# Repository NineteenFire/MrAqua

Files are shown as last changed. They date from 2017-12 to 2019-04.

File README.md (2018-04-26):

# MrAqua Aquarium Controller

This project was based off the iAqua controller written by Dan Cunningham with new features and updates here.

Controller home screen

## Features

- Water temperature monitoring
  - Allows calibration
  - Automatic shutoff of heater if water exceeds setpoint
- Automatic water top-off 
  - Float switch inputs for tank and reservoir
  - Set maximum run-time with alarm flagged if exceeded
- Feeding mode
  - Monitor time since last fed
  - Control outlets during feeding (ie turn off pumps)
- Light control 
  - 6-channel PWM or IR control of e-series LED
  - 4 lighting levels (moonlight, sunrise, mid-morning and full daylight)
- Dosing
  - 3 channels
  - Individual settings for each channel
- 8 power outlet control
  - Manual control or set on/off times
  - Aux outlets can be set to cycle times (ie on 10 minutes every 2 hours)

## Hardware

- Arduino Mega
- 320 x 240 LCD
- Arduino Mega TFT Shield (or custom shield below)
- 12V power supply
- 8 channel relay board
- DS18B20 temperature sensor
- Peristaltic pumps
- Float switch
- Submersible 12V pump
- (Optional)PCA9685 breakout board

## Libraries

- [Adafruit PWM Servo Driver](https://github.com/adafruit/Adafruit-PWM-Servo-Driver-Library)
- [Dallas Temperature](https://github.com/milesburton/Arduino-Temperature-Control-Library)
- [Time Library](https://github.com/PaulStoffregen/Time)
- [Arduino IR Remote](https://github.com/z3t0/Arduino-IRremote)
- [DS1307RTC](https://github.com/PaulStoffregen/DS1307RTC)
- [SdFat](https://github.com/greiman/SdFat)
- [TimeAlarms](https://github.com/PaulStoffregen/TimeAlarms)
- [UTFT](http://www.rinkydinkelectronics.com/library.php?id=51)
- [UTFT_SdRaw](https://platformio.org/lib/show/565/UTFT_SdRaw)
- [URTouch](http://www.rinkydinkelectronics.com/library.php?id=92)

## Setup

If you are using an ecoxotic e-series LED set "lightCSP" to true, otherwise set it to false.  If you are using a PCA9685 chip for PWM set boolean "PCA9685Installed" to true.

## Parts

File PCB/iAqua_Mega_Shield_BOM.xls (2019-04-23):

Designator | DK# | part_value | Quantity
IR1 |  | IR Transmitter | 1
U1 |  | Mega 2560 | 1
U2, U3, U4, U5, U6 | 296-26482-5-ND | 74HC541PW | 5
U12, U13 | 296-27172-1-ND | ULN2003ANSR | 2
C8, C13 | 311-1458-1-ND | 1u | 2
C12, C14 | 399-6098-ND | 47u | 2
Q3 | 475-1437-ND | SFH 300-3/4 | 1
C7 | 490-1799-1-ND | 2u2 | 1
U8 | 497-7253-1-ND | L7805ACD2T-TR | 1
U10 | 497-14661-1-ND | LDF33DT-TR | 1
U9 | 568-8366-5-ND | PCA9685 | 1
ATO, Fan1, Fan2, FloatSwitch1, FloatSwitch2, J2, Pump1, Pump2, Pump3 | 609-3918-ND | 2Pin Terminal Block | 9
P3, P4 | 609-3926-ND | 10Pin Terminal Block | 2
C1, C2, C3, C4, C5, C6, C9, C11 | 1276-1003-1-ND | 100n | 8
C10 | 1276-1123-1-ND | 330n | 1
B1 | 3001K-ND | 3001 | 1
D1, D7 | B340A-FDICT-ND | B340A-13-F | 2
Q4 | DMN3032LE-13DICT-ND | DMN3032LE-13 | 1
U7 | DS1307Z+T&RCT-ND | DS1307 | 1
U11 | MCP9701AT-E/TTCT-ND | MCP9701AT-E/TT | 1
Q1 | MMBT2222AFSCT-ND | MMBT2222A | 1
Q2 | MMBT2907AFSCT-ND | MMBT2907A | 1
R9, R10, R20, R22, R32, R33 | P1.0KACT-ND | 1K0 | 6
R1, R11 | P4.7KACT-ND | 4K7 | 2
R21 | P10ACT-ND | 10R0 | 1
R4, R5, R12, R13, R14, R15, R16, R24, R30, R34 | P10KACT-ND | 10K0 | 10
R2, R3, R28, R35, R36, R37, R38, R39, R40 | P100ACT-ND | 100R | 9
R27 | P100KACT-ND | 100K | 1
R23 | P499CCT-ND | 499R | 1
JP1 | S1011EC-03-ND | 3pin header | 1
P1, P2 | S1011EC-03-ND | 3pin header | 2
P10 | S1011EC-10-ND | 10Pin Header | 1
HD1, HS1, HS2 | S2012EC-18-ND, A113648-ND | 38 pin header, 40 pin single row header | 3
P9 | S6104-ND | PRPC020DAAN-RC | 1
Y1 | X1123-ND | ECS-3X8X | 1

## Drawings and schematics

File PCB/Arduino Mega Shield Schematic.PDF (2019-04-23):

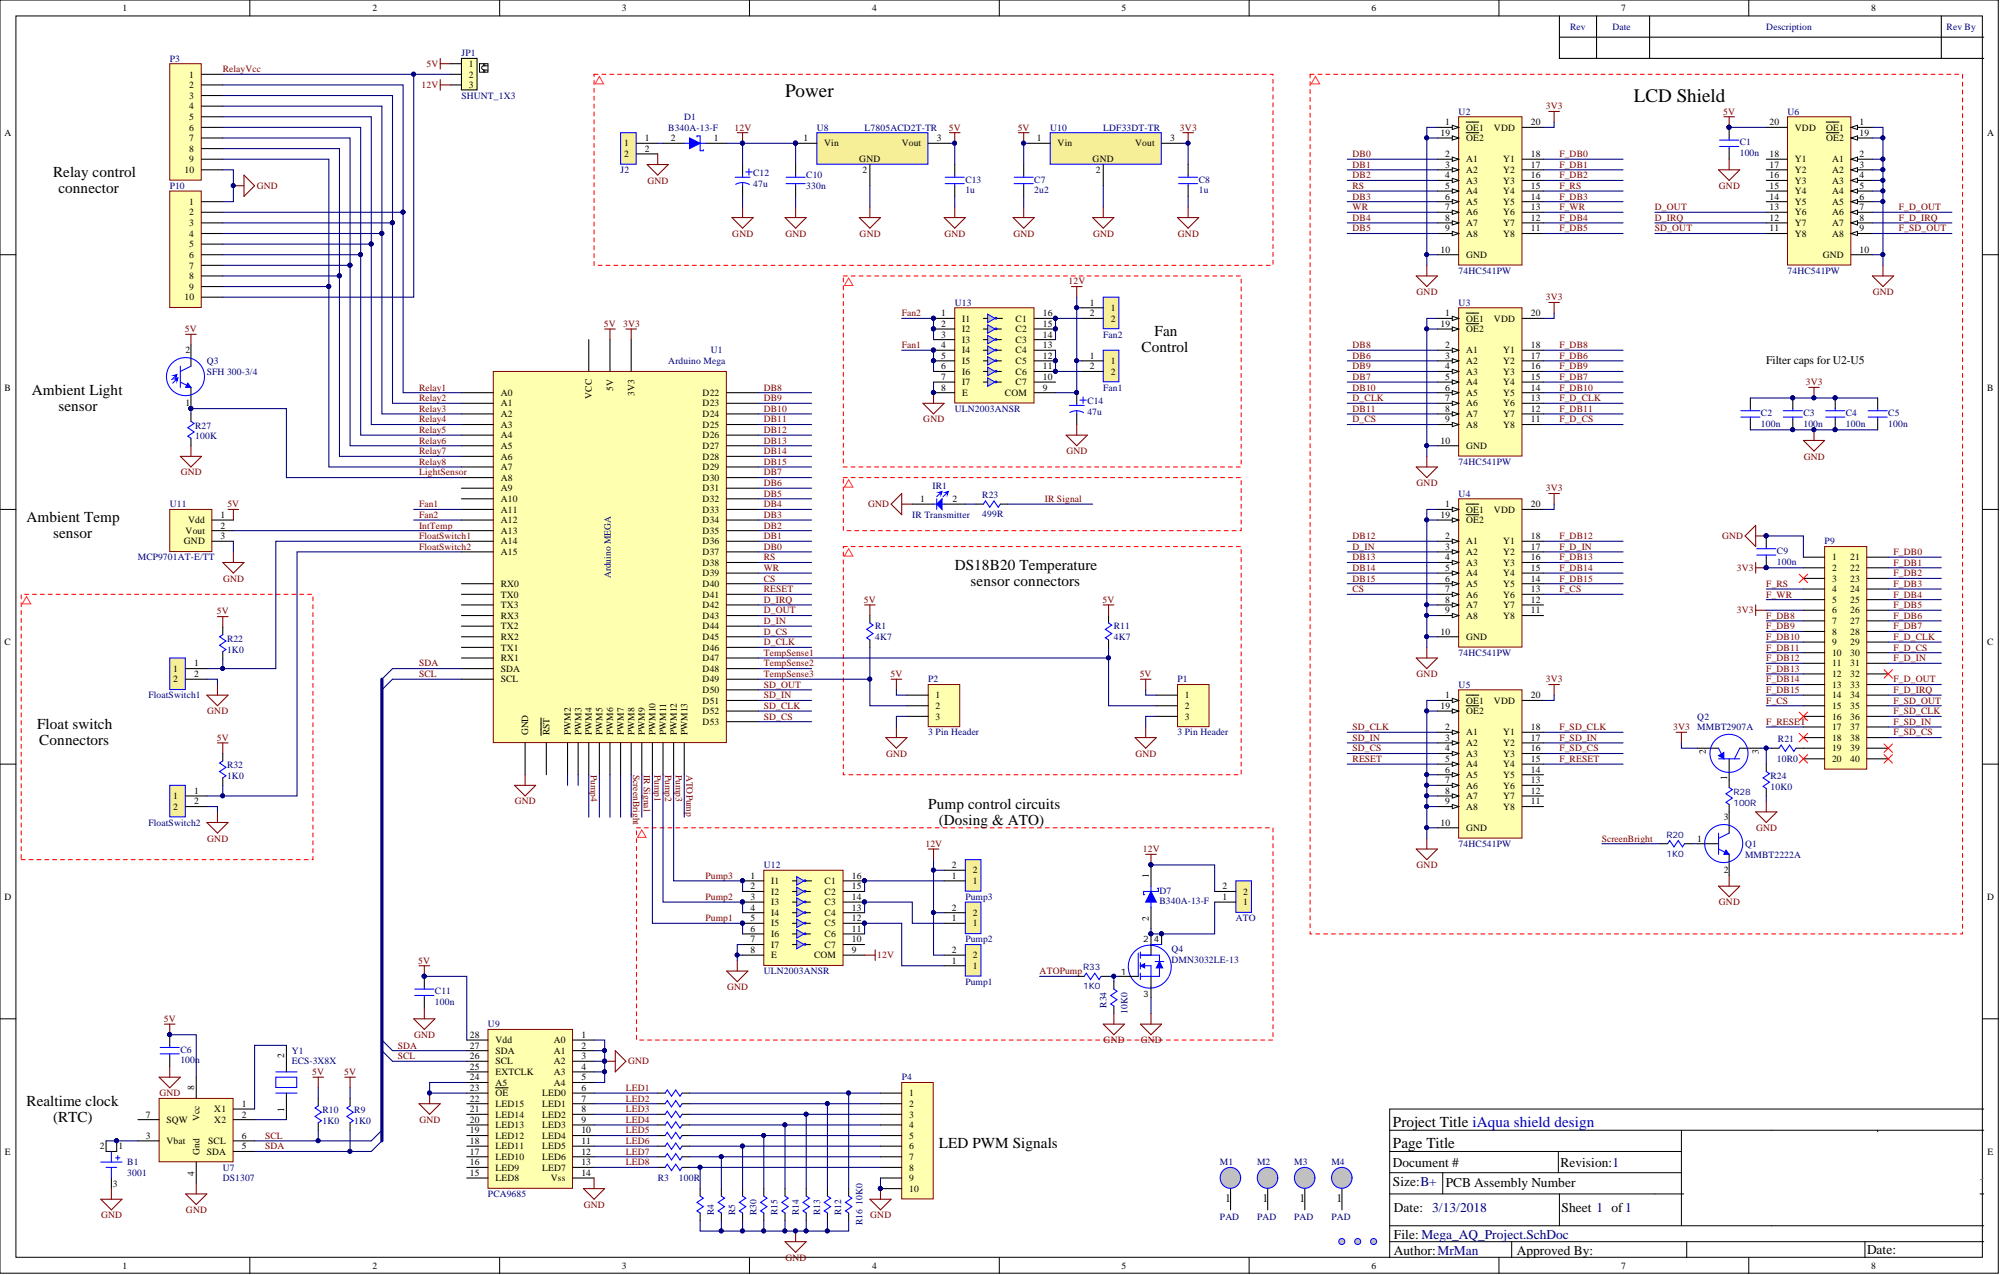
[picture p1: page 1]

2 | D R3 2 | SCL

Page Title | Del ta-Q Technologies Corp. 3755 Wi l l ingdon Bri t ish Columbi | Ave Burnaby a Canada, V5G 3H3 | CO NFIDENTIA PROPRIETARY

# | Revision: 1
B+ | PCB Assembly Number
Date: 3/13/2018 | Sheet 1 of 1 | The information contained in this dr awing is the sole prope rty of Delta -Q T e chnologie s Corp. Any r eproduction in whole or in pa rt without the written pe rmis sion of Delta -Q T e chnologie s Corp. is prohibite d

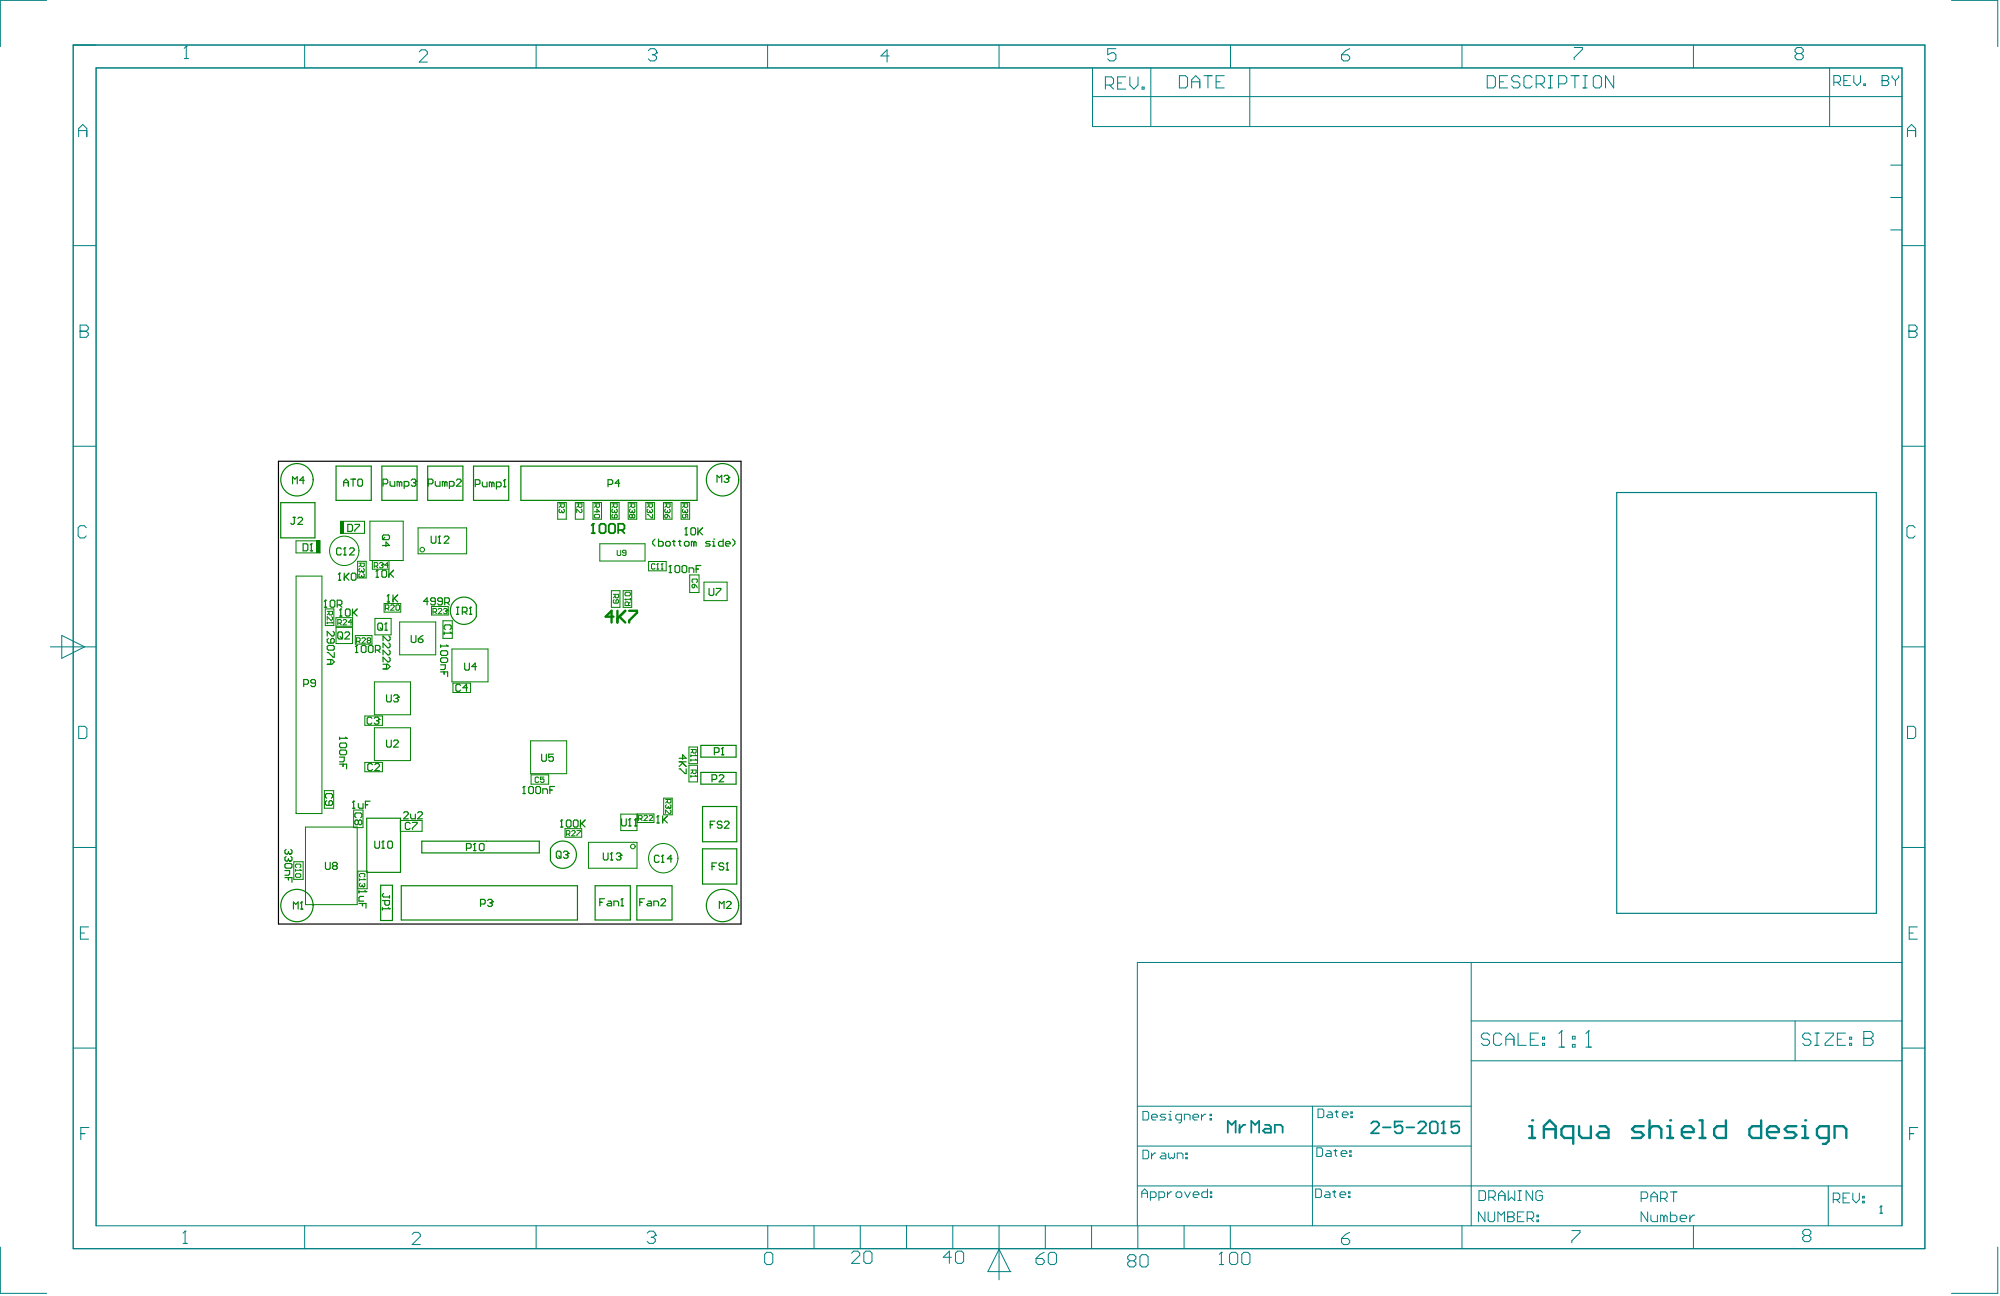
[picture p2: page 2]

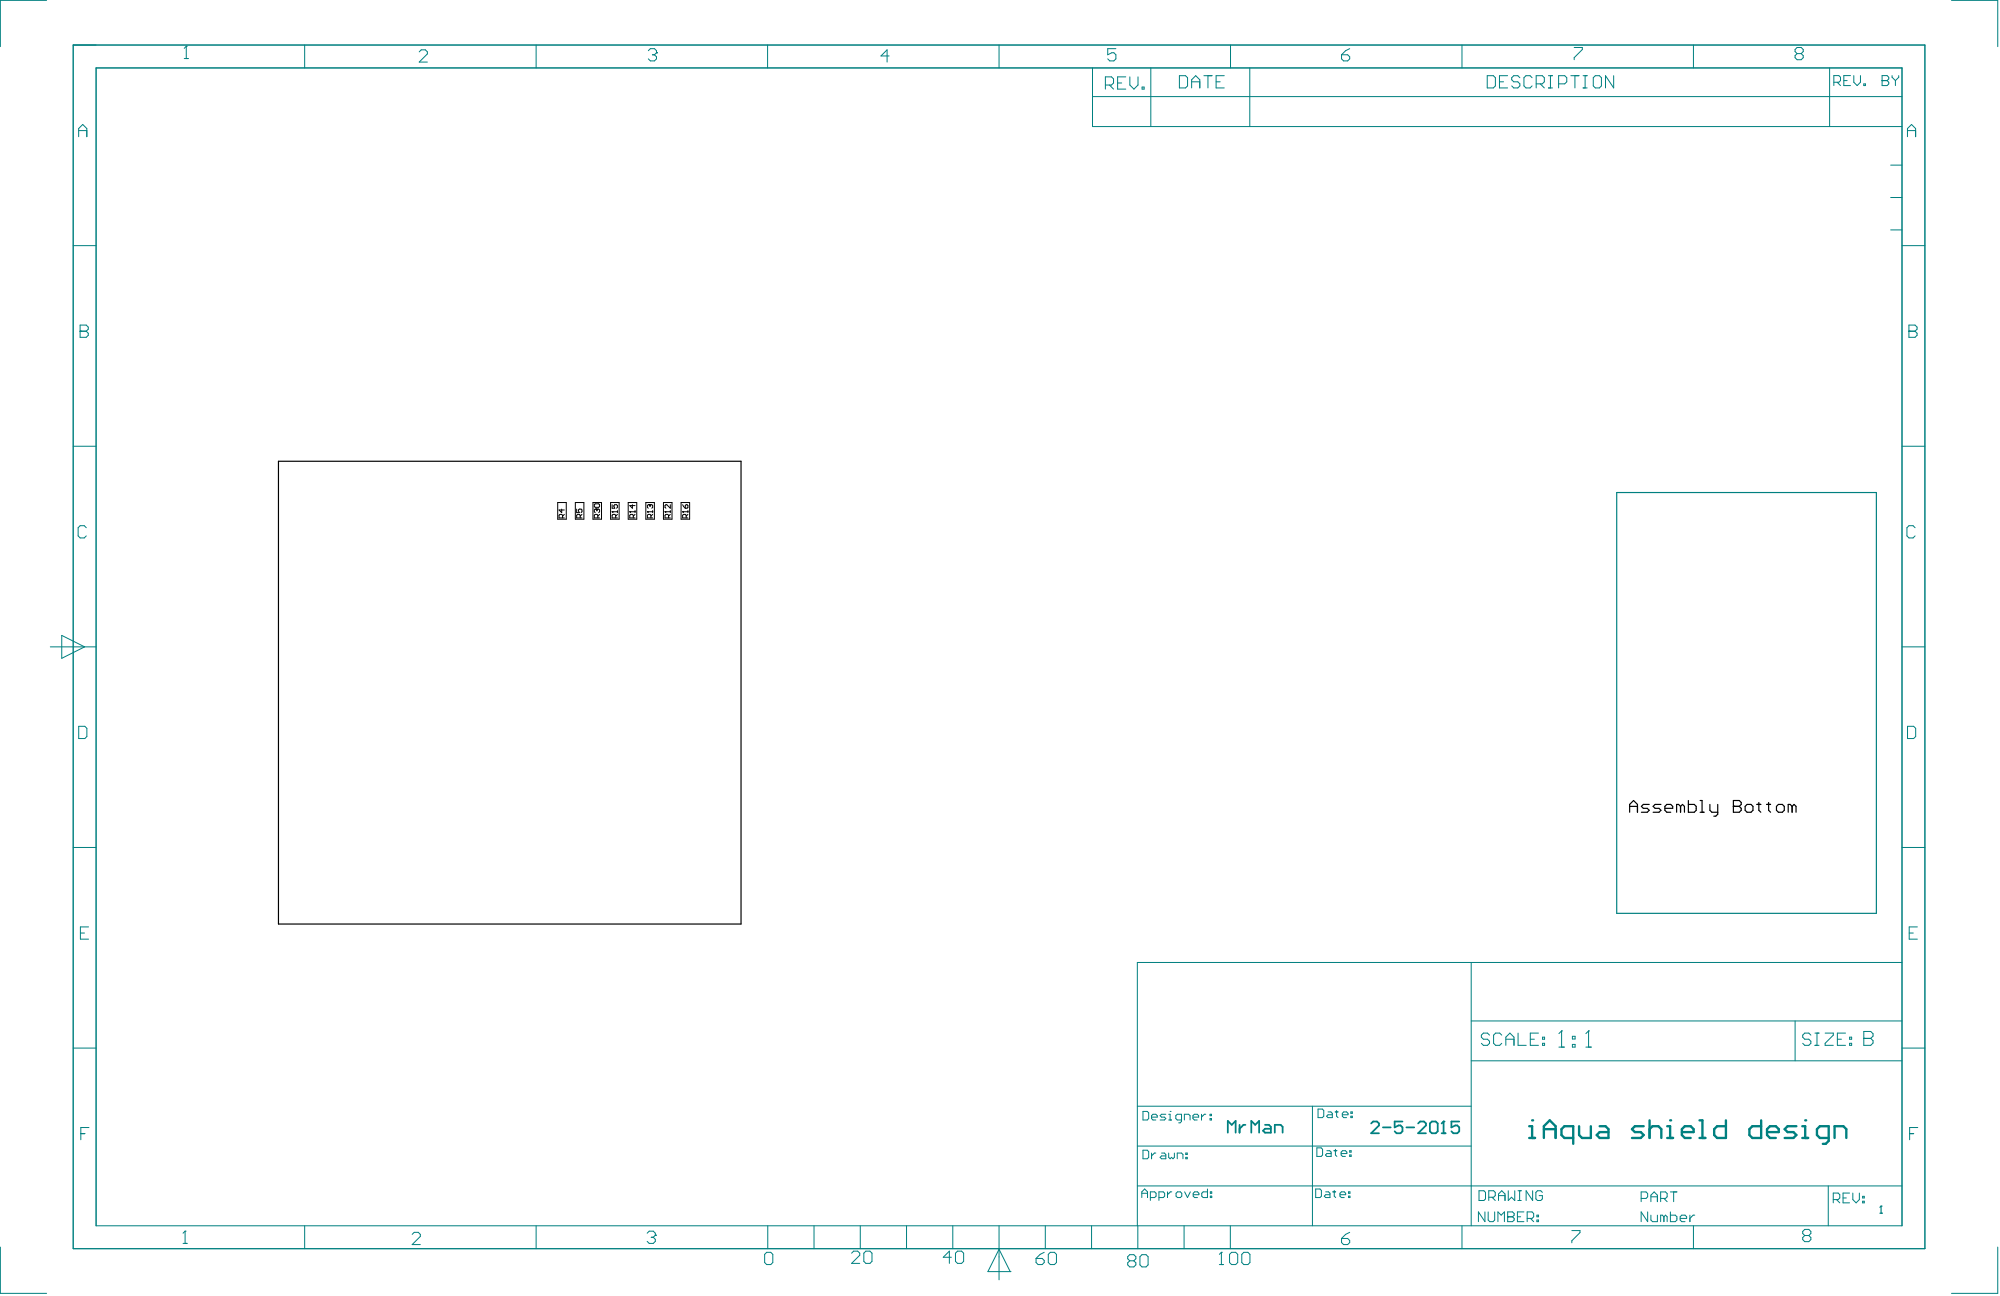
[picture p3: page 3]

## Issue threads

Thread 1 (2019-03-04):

Please include the PCB and BOM here

WZ9V, 2019-03-04:
It would be nice if the PCB and BOM files were here also instead of having to dig them out of the very long thread on PlantedTank.

NineteenFire, 2019-04-23:
Done

Closed 2019-04-23.

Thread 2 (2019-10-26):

Documentation/build thread?

Sokonomi, 2019-10-26:
Is there a thread somewhere that shows how to build this device?

rajdude, 2020-06-19:
I am also looking for the same information. I Googled this up and down but so far, have not found anything. Other than the original thread, which this code is based on there seems to be nothing out there

https://www.plantedtank.net/forums/20-diy/677265-iaqua-my-touch-interface-aquarium-controller-arduino.html

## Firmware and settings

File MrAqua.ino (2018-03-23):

/*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
 * 2. Redistributions in binary form must reproduce the above copyright
 *    notice, this list of conditions and the following disclaimer in the
 *    documentation and/or other materials provided with the distribution.

 * THIS SOFTWARE IS PROVIDED BY THE CONTRIBUTORS "AS IS" AND ANY EXPRESS OR 
 * IMPLIED WARRANTIES, INCLUDING, BUT NOT LIMITED TO, THE IMPLIED WARRANTIES 
 * OF MERCHANTABILITY AND FITNESS FOR A PARTICULAR PURPOSE ARE DISCLAIMED. IN
 * NO EVENT SHALL THE CONTRIBUTORS BE LIABLE FOR ANY DIRECT, INDIRECT, INCIDENTAL,
 * SPECIAL, EXEMPLARY, OR CONSEQUENTIAL DAMAGES (INCLUDING, BUT NOT LIMITED TO, 
 * PROCUREMENT OF SUBSTITUTE GOODS OR SERVICES; LOSS OF USE, DATA, OR PROFITS; OR 
 * BUSINESS INTERRUPTION) HOWEVER CAUSED AND ON ANY THEORY OF LIABILITY, WHETHER IN
 * CONTRACT, STRICT LIABILITY, OR TORT (INCLUDING NEGLIGENCE OR OTHERWISE)
 * ARISING IN ANY WAY OUT OF THE USE OF THIS SOFTWARE, EVEN IF ADVISED OF THE
 * POSSIBILITY OF SUCH DAMAGE.  
 */

// iAqua Aquarium Controller w/ iPhone-like Interface
// Written by Dan Cunningham, aka AnotherHobby @ plantedtank.net
// Various updates added by Ryan Truss, aka MrMan
// Much code was swiped, modified, and integrated or otherwise inspired from other public works
// All code is public domain, feel free to use, abuse, edit, and share
// Written for Arduino Mega 2560
//
// MrAqua v2.5.3
// -Fixed feeding restart button to only re-start timer
// -Updated screen setting menu to update brightness as it's changed rather than waiting till it
//  dims and then goes bright at a touch
//
// MrAqua v2.5.2
// -Updated feeding to allow not including outlets in feeding routine
// -Updated homescreen ATO display (empty reservoir shows as alarm instead of always displaying)
//
// MrAqua v2.5.0
// -Added watchdog to reset MCU on code freezing
// -Fixed bug where aux1 in timer mode would turn off aux2
// -Updated feeding screen/home screen to show exact time remaining instead of <x minutes
// -Swapped CO2 and Heater pin/icon locations, search for "swapped" to find all instaces and revert
// -Added code to use Serial2 to send/receive information from remote LED module (send LED values, 
//  fan state, reading LED heatsink temperature and request for LED values)
//
// MrAqua v2.4.0
// -Fix power schedule screen (45 degree text is unreadable)
// -Update auto-dimming to use an idle after x minutes timer instead of reading ambient light
// -Home screen now shows all 3 temperatures at the same time if more than just water sensor is enabled
//
// MrAqua v2.3.6
// -Add ability for Aux1 and Aux2 to be used as repeated timer rather than single 24Hr schedule
// -Updated some of the check boxes to on/off icon to fit with theme of the program
// -Updated power alarm behaviours during feeding to avoid devices turning on/off when they shouldn't
//
// MrAqua v2.3.5
// -Fixed startup where outputs would be ON but display showing them OFF
// -Added manual ATO turn-on by pressing section on home screen (runs for max run time)
//
// MrAqua v2.3.3 / 2.3.4
// -Fixed some bugs including heatsink temp sensor using wrong pin, dosing amount limits and PCB temp 
//  sensor not able to read in degrees F
//
// MrAqua v2.3.2
// -Added seperate screen function for IR lights using up/down arrows
// -Dosing alarms now trigger the start but main loop turns them off.  This way the program doesn't
//  freeze when it starts to dose
// -Corrected heatsink temp sensor to use correct device address
//
// MrAqua v2.3.1
// -Added code from alphabeta to add a second on/off schedule for lights
// -Updated light values/system so stored values are always 0-100
// -Updated home screen dosing to correctly draw tubes and not allow remaining volume to go below 0
//
// MrAqua 
// -Updated feeding routine to only toggle filter/pump/aux outputs
// -Added graph display for LED channels 
// -Added routine writeToLED(channel,value) to handle writing to either PCA or Mega PWM pins
// -Modified LED PWM code to optionally use PCA9685 for 12-bit dimming
// -Added 5th/6th LED channel, moved EEPROM for LED values to 400's
// -Added lunar cycle control
// -Added probe settings menu to enable/disable temp sensors and change display units between C and F
// -Added sub-settings menus for sensors to control when fans turn on/off (external fan 
//  controlled by heatsink sensor, internal fan controlled by internal temp) or heater in case of
//  probe 1.  Also added calibration offset for probes
// -Changed feeding, update time and screen dim tracking to using RTC instead of millis 
//  (millis only used for tracking touch timing for better resolution)
// -Changed code for 3 pumps, reworked schedule and setting screens to select a pump and then
//  individual pump dose amounts
// -Added code for ATO
// -Changed LED color setting to bargraph (0-100%) instead of up/down button
// -Added color setting menu for changing bargraph colors
// -Added routine for sending commands to sat+ with the updated bargraphs
// -switched RTClib to DS1307RTC library
// -switched to sdfat and utft_sdraw library for accessing SD card files (can use larger SD 
//  cards and has faster loading speeds)
// -Added read of displayInCelcius to startup
// -Added boolean displayIn12Hr to change clock to 24Hr/12Hr
//
// Original iAqua revision documentation:
// CURRENT VERSION 1.0.4
// - the smart startup routine has been reworked and fixed by robsworld78 at The Planted Tank forums!
// - added a first run routine that will zero out all EEPROM data that is needed by iAqua
//
// VERSION 1.0.3
// - fixed smartstartup routine bugs
// - fixed dosing display when resevoir goes negative due to forgettig to hit fill
// - added robsworld78 at The Planted Tank's PWM smart startup lighting code
// - fixed issue when temp turned red, and then turned feeding time red
//
// VERSION:  1.0.2
// - more accurate math for how doses were calcualted on home screen
// - updated power schedules to update home screen immediately
// - day name was off using new RTC and Time library
//
// VERSION:  1.0.1
// - created smart startup routine
// - fixed math bug with dosing pump speed saving to eeprom
// - changed PWM pins for dosing pumps to make room for RGBW PWM pins
// - changed from previous RTC library to RTClib.h
//
// VERSION:  1.0
// - initial version
//
// EEPROM locations (saved settings)
// SPACE // DESCRIPTION
// 0 // 
// 1 // feeding enable filter
// 2 // feeding enable circ
// 3 // feeding enable heat
// 4 // feeding enable co2
// 5 // feeding enable aux 1
// 6 // feeding enable aux 2
// 7 // feeding minutes setting
// 8 // feeding  light 1 (0 off, 1 on)
// 9 // feeding pwr light 2 (0 off, 1 on)
// 10 // feeding pwr filter (0 off, 1 on)
// 11 // feeding pwr circ (0 off, 1 on)
// 12 // feeding pwr heat (0 off, 1 on)
// 13 // feeding pwr co2 (0 off, 1 on)
// 14 // feeding pwr aux 1 (0 off, 1 on)
// 15 // feeding pwr aux 2 (0 off, 1 on)
// 16 // NOT USED
// 17 // heater off temp
// 18 // heater on temp
// 19 // NOT USED
// 20 // pump 1 dose in mL
// 21 // pump 2 dose in mL
// 22 // pump 3 dose in mL
// 23 // pump 1 sec/ml
// 24 // pump 2 sec/ml
// 25 // pump 3 sec/ml
// 26 // dosing reseviors capacity in mL
// 27 // 
// 28 // screen:  return home
// 29 // screen:  autodim level
// 30 // screen:  autodim seconds
// 31 // screen:  brightness if no dim
// 32 // pump 1 remaining volume high byte ^10th
// 33 // pump 1 remaining volume low byte
// 34 // pump 2 remaining volume high byte ^10th
// 35 // pump 2 remaining volume low byte
// 36 // pump 3 remaining volume high byte ^10th
// 37 // pump 3 remaining volume low byte
// ... //
// 40 // ATO Enabled
// 41 // Reservoir switch Enabled
// 42 // Low level wait time in minutes
// 43 // Max run-time / 10
// 44 // ATO alarm flagged
// ... //
// 50 // Temp sensor 1 installed (water)
// 51 // Temp sensor 2 installed (heatsink)
// 52 // Internal sensor installed (MCP9701)
// 53 // Heatsink fan on temperature
// 54 // Heatsink fan off temperature
// 55 // Internal fan on temperature
// 56 // Internal fan off temperature
// 57 // Display in celcius?
// 58 // sensor 1 calibration offset
// 59 // sensor 2 calibration offset
// 60 // sensor 3 calibration offset
// 61 // display sensor 1 on home screen
// 62 // display sensor 2 on home screen
// 63 // display sensor 3 on home screen
// ... // 
// 70 // Lunar cycle enabled
// 71 // Clouds enabled
// 72 // Cloud start hour
// 73 // Cloud start minute
// 74 // Cloud run hours
// 75 // Cloud run minutes
// 76 // Cloud channels enabled (bit 0 = chan1, bit 1 = chan2...)
// ... //
// 80 // bar 1 color
// 81 // bar 2 color
// 82 // bar 3 color
// 83 // bar 4 color
// 84 // bar 5 color
// 85 // bar 6 color
// 86 // bar 7 color
// 87 // bar 8 color
// 88 // bar 9 color
// ... //
// 100-139 // power scheudle
// 220-243 // light ramp schedule
// 280-284 // light bar colors
// 300 // pump1 onHour
// 301 // pump1 onMin
// 302 // pump1 SUN
// 303 // pump1 MON
// 304 // pump1 TUE
// 305 // pump1 WED
// 306 // pump1 THUR
// 307 // pump1 FRI
// 308 // pump1 SAT
// 309-317 // pump2
// 318-326 // pump3
// ... //
// 400+ // LED values

#include <avr/wdt.h> //added for WDT
#include <Wire.h> // needed by tons of stuff
#include <EEPROM.h>  // used to store and retrieve settings from memory
#include <UTFT.h>  // used to interface with the TFT display
#include <SdFat.h>
#include <UTFT_SdRaw.h>
#include <URTouch.h>  // used to interface with the touch controller on the TFT display
#include <DS1307RTC.h>
//#include <DS3232RTC.h>
#include <TimeLib.h>
#include <TimeAlarms.h>  // used to power schedules
#include <IRremote.h>  // used to send IR commands to the light, LED must be on pin 9
#include <OneWire.h> // network library to communicate with the DallasTemperature sensor, 
#include <DallasTemperature.h>  // library for the Temp sensor itself
#include <Adafruit_PWMServoDriver.h> //PCA9865

UTFT myGLCD(SSD1289,38,39,40,41); // start up an instance of the TFT screen
URTouch myTouch(46,45,44,43,42);  // start up an instance of for touch
//URTouch myTouch(6, 5, 4, 3, 2); // For standard TFT shield

// file system object
SdFat sd;
const byte ChipSelect = 53; // For TFT Shield
UTFT_SdRaw myFiles(&myGLCD);

// Declare which fonts we will be using
extern uint8_t Sinclair_S[];
extern uint8_t arial_bold[];

//initialize PCA9865
Adafruit_PWMServoDriver pwm = Adafruit_PWMServoDriver(0x40);

// define relay pins
const int pwrLight1Pin = A0;
const int pwrLight2Pin = A1;
const int pwrFilterPin = A2;
const int pwrCircPin = A3;
//const int pwrHeatPin = A4;  //normal operation
//const int pwrCO2Pin = A5;   //normal operation
const int pwrHeatPin = A5;//co2/heater pins swapped
const int pwrCO2Pin = A4; //co2/heater pins swapped
const int pwrAux1Pin = A6;
const int pwrAux2Pin = A7;

//define misc pins
const int lightSensorPin = A8;  // analog pin for the ambient light sensor
const int pressureSensorPin = A9;  // analog pin for the CO2 pressure sensor
const int fan1Pin = A11;
const int fan2Pin = A12;
const int internalTempPin = A13;
const int ATOFloatPin = A14;
const int TankFloatPin = A15;
const int screenBrightPin = 8; // pwm pin for the LCD backlight
//define pump pins
const int dosingPump1 = 10;
const int dosingPump2 = 11;
const int dosingPump3 = 12;
const int ATOPumpPin = 13;
// define RGBW PWM pins
const int led1Pin = 2;
const int led2Pin = 3;
const int led3Pin = 4;
const int led4Pin = 5;
const int led5Pin = 6;
const int led6Pin = 7;

// Pins for temperature sensor
#define ONE_WIRE_BUS_W 47  //water sensor on pin 47
#define ONE_WIRE_BUS_H 49  //Heatsink sensor on pin 49

// Setup a oneWire instance to communicate with any OneWire devices
OneWire oneWireW(ONE_WIRE_BUS_W);
OneWire oneWireH(ONE_WIRE_BUS_H);

// Pass our oneWire reference to Dallas Temperature. 
DallasTemperature sensorW(&oneWireW);
DallasTemperature sensorH(&oneWireH);

// Device address variables
DeviceAddress waterSensor;
DeviceAddress heatsinkSensor;

// create an IR instance
IRsend irsend;

byte dispScreen=0;    // screens are listed below
//1-home
//    2-feeding
//    3-power
//    4-settings
//        5 - Light Settings
//        6 - clock
//        7 - feed settings
//        18- sensor settings
//            8 - heater settings
//            19- heatsink fan settings
//            20- internal fan settings
//        9 - Schedule
//            11 - Power schedule
//                12 - Power item
//            15 - Dosing
//            13 - Light ramps schedule screen
//                14 - light ramp schedule
//        10 - Dosing settings (index 1-3 for pump#)
//        16 - Screen settings
//        17 - ATO settings
//        21 - Lunar settings
//        22 - Light bargraph color settings
//        23 - LED graph
//        24 - Light Settings for IR lights

byte scheduleItem; // track which item is being scheduled
byte currentLightMode=0;  //0=high sun, 1=mid sun, 2=low sun, 3=moon, 4=transition, 5=unknown
byte lightEditing=0;  // track if we are actively editing lights

// the next 5 variables will be set at the start of a lighting fade
int fadeDurationSeconds = 0; 
unsigned long fadeStartingSeconds = 0;
unsigned long fadeTimeLeft;
boolean fadeInProgress = false;
byte fadeFromMode = 0;  //0=high sun, 1=mid sun, 2=low sun, 3=moon
byte fadeToMode = 0;  //0=high sun, 1=mid sun, 2=low sun, 3=moon

struct RGBW // for storing light intensity values
{
  unsigned int chan1;
  unsigned int chan2;
  unsigned int chan3;
  unsigned int chan4;
  unsigned int chan5;
  unsigned int chan6;
};
typedef struct RGBW LightColor;

LightColor currentColor = {
  0,0,0,0,0,0}; // The current color of the light (used for fading)
LightColor lastColor = {
  0,0,0,0,0,0};   // The previous color of the light (used for fading)
LightColor targetColor = {
  0,0,0,0,0,0}; // The target color of the light (used for fading)
LightColor tempColor = {
  0,0,0,0,0,0}; // The temporary color of the light (used for updating sat+)

LightColor lightHighSun = {
  0,0,0,0,0,0}; // store the RGBW values for the CS+ M1 button
LightColor lightMidSun = {
  0,0,0,0,0,0}; // store the RGBW values for the CS+ M2 button 
LightColor lightLowSun = {
  0,0,0,0,0,0}; // store the RGBW values for the CS+ M3 button 
LightColor lightMoon = {
  0,0,0,0,0,0}; // store the RGBW values for the CS+ M4 button 
  
//red, green, blue, white, yellow, violet, aqua
const unsigned int VGAColor[] = {0xF800, 0x07E0, 0x001F, 0xFFFF, 0xFFE0, 0xF81F, 0x07FF};

//store colours for bargraphs
byte barColors[6] = {0,1,2,3,4,5};
byte selectedChan = 0; // used for tracking which channel is selected when changing colors

// used for time
tmElements_t prevRTC, saveRTC;
boolean displayIn12Hr = true;

// used for storing power states of relays
struct PWR
{  
  byte pwrLight1;
  byte pwrLight2;
  byte pwrFilter;
  byte pwrCirc;
  byte pwrHeat;
  byte pwrCO2;
  byte pwrAux1;
  byte pwrAux2;
} 
feedPower, preFeedPower, globalPower;

// used for storing power states of relays
struct FEED
{  
  byte pwrLight1;
  byte pwrLight2;
  byte pwrFilter;
  byte pwrCirc;
  byte pwrHeat;
  byte pwrCO2;
  byte pwrAux1;
  byte pwrAux2;
} 
feedSetting;

// holds the schedule for power relays and light ramping
struct PWRSCHED
{  
  byte active;
  byte onHour;
  byte onMinute;
  byte offHour;
  byte offMinute;
  byte timer;
}
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
void loop()
{
  unsigned long currentMillis = millis(); // get current millis
  time_t currentTime = now();

  //check temperature every 10 seconds
  if(now() - lastUpdateTime >= 10)
  {
    lastUpdateTime=now();
    checkTemp();
  }
  //check ATO/feeding and update time once per second
  if(now() != lastCheckTime)
  {
    lastCheckTime=now();
    updateTimeDate(false);//passing false results in updating screen only if time or date has changed
    checkATO();
    checkFeeding();
  }
  
  //Check status of current light ramp if applicable
  checkLightRamp();
  
  // check for touch events
  if (myTouch.dataAvailable())
  {
    if (currentMillis - prevMillisTouch > touchWaitTime) // make sure it's been .X sec between touches
    {
      // set backlight touch if not already set and turn up brightness
      if (backlightTouch==false) // backlight touch is for adjusting brightness after touch
      {
        Serial.println(F("Setting backlight to Bright value"));
        backLight = map(screenBrightMem,1,10,10,255);
        analogWrite(screenBrightPin, backLight);
        backlightTouch=true;
      }
      prevMillisTouch=currentMillis; // reset the touch timer
      dimTime = currentTime; // reset screen dim timer
      homeTime = currentTime; // reset return home timer
      processMyTouch();
    }
  }
  
  // adjust brightness automatically unless touch event
  unsigned long pastSeconds;
  if (screenDimSec!=0) // if set to 0, we won't dim
  {
    if (screenDimLevel!=0) // if set to 0, we won't dim
    {
      if (backlightTouch==true)
      {
        pastSeconds = (currentTime - dimTime);
        if (pastSeconds > screenDimSec)
        {
          Serial.println(F("Reducing backlight to dim level"));
          backlightTouch=false;
          idleBrightness();
        }
      }
    }
  }

  // if we aren't on the home or feeding screen, we return after preset time of no interaction
  if (screenRetHome != 0) // if set to 0, we don't return home
  {
    if ((dispScreen!=1)&&(dispScreen!=2))
    {
      pastSeconds = (currentTime - homeTime);
      if (pastSeconds > (60*screenRetHome)) 
      {
        Serial.println(F("Returning to home"));
        if (dispScreen==9) updateAlarms(); // this will rebuild all of the schedules
        if (dispScreen==5)
        {
          smartStartupRamp();
          setStartupLighting();
        }
        screenHome();
        touchWaitTime = LONG_WAIT;
      }
    }
  }
  
  //Check dosing pumps
  if(pump1State)
  {
    if(currentMillis > pump1StartMillis + pump1millis)
    {
      pump1State = false;
      analogWrite(dosingPump1, 0);
      Serial.print(F("Pump1 done.\n"));
      if(dispScreen == 10)myFiles.load(92, 170, 48, 48, "10test.raw",2);
    }
  }
  if(pump2State)
  {
    if(currentMillis > pump2StartMillis + pump2millis)
    {
      pump2State = false;
      analogWrite(dosingPump2, 0);
      Serial.print(F("Pump2 done.\n"));
      if(dispScreen == 10)myFiles.load(92, 170, 48, 48, "10test.raw",2);
    }
  }
  if(pump3State)
  {
    if(currentMillis > pump3StartMillis + pump3millis)
    {
      pump3State = false;
      analogWrite(dosingPump3, 0);
      Serial.print(F("Pump3 done.\n"));
      if(dispScreen == 10)myFiles.load(92, 170, 48, 48, "10test.raw",2);
    }
  }
  //Check aux1/2 timers
  if(aux1TimerState)
  {
    if(currentMillis > (aux1TimerStart + aux1TimerFinish))
    {
      AlarmPwrAux1_Off();
      aux1TimerState = false;
      Serial.println(F("Aux1 timer finished."));
    }
  }
  if(aux2TimerState)
  {
    if(currentMillis > (aux2TimerStart + aux2TimerFinish))
    {
      AlarmPwrAux2_Off();
      aux2TimerState = false;
      Serial.println(F("Aux2 timer finished."));
    }
  }
  
  Alarm.delay(10); // must use Alarm delay to use the TimeAlarms library
  doggieTickle();
  /*
  //Parse command/requests from light fixture (only expect TEMP-XX.XX or 
  //LEDValues request at this point)
  if(Serial2.available())
  {
    //if we have received data read it into input char array
    byte size = Serial2.readBytes(input, INPUT_SIZE);
    input[size] = 0;
    char* separator = strchr(input, '-');
    //Check to see if message is incoming data
    if (separator != 0)
    {
      //Received data, actually split the string in 2, replace '-' with 0 and 
      //increase separator to point at the actual value
      *separator = 0;
      ++separator;
      String command = "";
      command.reserve(10);
      command = input;
      
      Serial.print(F("Parameter received: "));
      Serial.println(command);
      
      //do a case structure based on command
      if(command == "TEMP")
      {
        //received value of heatsink temperature
        temperature2 = atof(separator);
        Serial.print(F("Temperature2: "));
        Serial.println(temperature2);
      }
    }
    //check to see if message is a request
    separator = strchr(input, '?');
    if (separator != 0)
    {
      *separator = 0;
      ++separator;
      String request = "";
      request.reserve(10);
      request = input;
      
      Serial.print(F("Request received: "));
      Serial.println(request);
      
      if(request == "LEDValues")
      {
        //received request for all LED channel values
        Serial.println(F("Sending LED values"));
        writeToLED(1,currentColor.chan1);
        writeToLED(2,currentColor.chan2);
        writeToLED(3,currentColor.chan3);
        writeToLED(4,currentColor.chan4);
        writeToLED(5,currentColor.chan5);
        writeToLED(6,currentColor.chan6);
      }
    }
  }*/
  //End Serial2 monitoring
}

void checkLightRamp()
{
  // check on the fading of the lights  
  time_t currentTime = now();
  if(fadeInProgress == true)
  {
    if(currentTime > fadeStartingSeconds + fadeDurationSeconds)   // if we have just finished the fade...
    {
      fadeInProgress = false;
      currentLightMode = fadeToMode;  // If a color fade has been completed, set the final mode
      
      if(lightCSP==true) // for the CSP, we send a hard code to lock in the setting and avoid drift
      {
        // send IR command for correct lighting mode
        if (currentLightMode == 0) irsend.sendNEC(M1,32);
        else if (currentLightMode == 1) irsend.sendNEC(M2,32);
        else if (currentLightMode == 2) irsend.sendNEC(M3,32);
        else if (currentLightMode == 3) irsend.sendNEC(M4,32);
      }
      if(dispScreen==1) screenHome(); // redraw the home screen if we are home
    }
    else   // if the fade is still running
    {
      // If there is a fade in progress, check if there are any IR commands that should be sent
      checkLightFade((currentTime - fadeStartingSeconds), fadeDurationSeconds);
    }
  }
}
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

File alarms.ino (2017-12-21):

void updateAlarms()
{
  // clear, free, delete all possible alarms
  for (byte i=0; i<=50; i++) Alarm.free(i);

  //////// POWER ALARMS ////////
  if (schedLights1.active==1)
  {
    Alarm.alarmRepeat(schedLights1.onHour,schedLights1.onMinute,0,AlarmPwrLight1_On);
    Alarm.alarmRepeat(schedLights1.offHour,schedLights1.offMinute,0,AlarmPwrLight1_Off);
  }
  if (schedLights1s2.active==1)
  {
    Alarm.alarmRepeat(schedLights1s2.onHour,schedLights1s2.onMinute,0,AlarmPwrLight1_On);
    Alarm.alarmRepeat(schedLights1s2.offHour,schedLights1s2.offMinute,0,AlarmPwrLight1_Off);
  }
  if (schedLights2.active==1)
  {
    Alarm.alarmRepeat(schedLights2.onHour,schedLights2.onMinute,0,AlarmPwrLight2_On);
    Alarm.alarmRepeat(schedLights2.offHour,schedLights2.offMinute,0,AlarmPwrLight2_Off);
  }
  if (schedLights2s2.active==1)
  {
    Alarm.alarmRepeat(schedLights2s2.onHour,schedLights2s2.onMinute,0,AlarmPwrLight2_On);
    Alarm.alarmRepeat(schedLights2s2.offHour,schedLights2s2.offMinute,0,AlarmPwrLight2_Off);
  }
  if (schedCirc.active==1)
  {
    Alarm.alarmRepeat(schedCirc.onHour,schedCirc.onMinute,0,AlarmPwrCirc_On);
    Alarm.alarmRepeat(schedCirc.offHour,schedCirc.offMinute,0,AlarmPwrCirc_Off);
  }
  if (schedCo2.active==1)
  {
    Alarm.alarmRepeat(schedCo2.onHour,schedCo2.onMinute,0,AlarmPwrCO2_On);
    Alarm.alarmRepeat(schedCo2.offHour,schedCo2.offMinute,0,AlarmPwrCO2_Off);
  }
  if (schedAux1.active==1)
  {
    if(schedAux1.timer==0)
    {
      Alarm.alarmRepeat(schedAux1.onHour,schedAux1.onMinute,0,AlarmPwrAux1_On);
      Alarm.alarmRepeat(schedAux1.offHour,schedAux1.offMinute,0,AlarmPwrAux1_Off);
    }else
    {
      Alarm.timerRepeat(schedAux1.onHour,schedAux1.onMinute,0,AlarmPwrAux1_Timer);
    }
  }
  if (schedAux2.active==1)
  {
    if(schedAux1.timer==0)
    {
      Alarm.alarmRepeat(schedAux2.onHour,schedAux2.onMinute,0,AlarmPwrAux2_On);
      Alarm.alarmRepeat(schedAux2.offHour,schedAux2.offMinute,0,AlarmPwrAux2_Off);
    }else
    {
      Alarm.timerRepeat(schedAux2.onHour,schedAux2.onMinute,0,AlarmPwrAux2_Timer);
    }
  }

  //////// RAMP ALARMS ////////
  Alarm.alarmRepeat(ramp1.onHour,ramp1.onMinute,0,AlarmRamp1);
  Alarm.alarmRepeat(ramp2.onHour,ramp2.onMinute,0,AlarmRamp2);
  Alarm.alarmRepeat(ramp3.onHour,ramp3.onMinute,0,AlarmRamp3);
  Alarm.alarmRepeat(ramp4.onHour,ramp4.onMinute,0,AlarmRamp4);
  Alarm.alarmRepeat(ramp5.onHour,ramp5.onMinute,0,AlarmRamp5);
  Alarm.alarmRepeat(ramp6.onHour,ramp6.onMinute,0,AlarmRamp6);
  
  //////// Ramp PWM to 0, 4 hours after ramp6 ////////
  byte zeroHour = ((ramp6.onHour + 4) % 24);
  byte zeroMin = ramp6.onMinute;
  Alarm.alarmRepeat(zeroHour,zeroMin,0,rampToZero);
  
  //////// DOSING ALARMS ////////
  if (pump1.Sunday==1)
  {
    Alarm.alarmRepeat(dowSunday, pump1.onHour,pump1.onMinute,0,AlarmMacros);
  }
  if (pump2.Sunday==1)
  {
    Alarm.alarmRepeat(dowSunday, pump2.onHour,pump2.onMinute,0,AlarmMicros);
  }
  if (pump3.Sunday==1)
  {
    Alarm.alarmRepeat(dowSunday, pump3.onHour,pump3.onMinute,0,AlarmExcel);
  }
  if (pump1.Monday==1)
  {
    Alarm.alarmRepeat(dowMonday, pump1.onHour,pump1.onMinute,0,AlarmMacros);
  }
  if (pump2.Monday==1)
  {
    Alarm.alarmRepeat(dowMonday, pump2.onHour,pump2.onMinute,0,AlarmMicros);
  }
  if (pump3.Monday==1)
  {
    Alarm.alarmRepeat(dowMonday, pump3.onHour,pump3.onMinute,0,AlarmExcel);
  }
  if (pump1.Tuesday==1)
  {
    Alarm.alarmRepeat(dowTuesday, pump1.onHour,pump1.onMinute,0,AlarmMacros);
  }
  if (pump2.Tuesday==1)
  {
    Alarm.alarmRepeat(dowTuesday, pump2.onHour,pump2.onMinute,0,AlarmMicros);
  }
  if (pump3.Tuesday==1)
  {
    Alarm.alarmRepeat(dowTuesday, pump3.onHour,pump3.onMinute,0,AlarmExcel);
  }
  if (pump1.Wednesday==1)
  {
    Alarm.alarmRepeat(dowWednesday, pump1.onHour,pump1.onMinute,0,AlarmMacros);
  }
  if (pump2.Wednesday==1)
  {
    Alarm.alarmRepeat(dowWednesday, pump2.onHour,pump2.onMinute,0,AlarmMicros);
  }
  if (pump3.Wednesday==1)
  {
    Alarm.alarmRepeat(dowWednesday, pump3.onHour,pump3.onMinute,0,AlarmExcel);
  }
  if (pump1.Thursday==1)
  {
    Alarm.alarmRepeat(dowThursday, pump1.onHour,pump1.onMinute,0,AlarmMacros);
  }
  if (pump2.Thursday==1)
  {
    Alarm.alarmRepeat(dowThursday, pump2.onHour,pump2.onMinute,0,AlarmMicros);
  }
  if (pump3.Thursday==1)
  {
    Alarm.alarmRepeat(dowThursday, pump3.onHour,pump3.onMinute,0,AlarmExcel);
  }
  if (pump1.Friday==1)
  {
    Alarm.alarmRepeat(dowFriday, pump1.onHour,pump1.onMinute,0,AlarmMacros);
  }
  if (pump2.Friday==1)
  {
    Alarm.alarmRepeat(dowFriday, pump2.onHour,pump2.onMinute,0,AlarmMicros);
  }
  if (pump3.Friday==1)
  {
    Alarm.alarmRepeat(dowFriday, pump3.onHour,pump3.onMinute,0,AlarmExcel);
  }
  if (pump1.Saturday==1)
  {
    Alarm.alarmRepeat(dowSaturday, pump1.onHour,pump1.onMinute,0,AlarmMacros);
  }
  if (pump2.Saturday==1)
  {
    Alarm.alarmRepeat(dowSaturday, pump2.onHour,pump2.onMinute,0,AlarmMicros);
  }
  if (pump3.Saturday==1)
  {
    Alarm.alarmRepeat(dowSaturday, pump3.onHour,pump3.onMinute,0,AlarmExcel);
  }
  Serial.print(F("# of alarms: "));
  Serial.println(Alarm.count());
}

//===Light1 routines===

void AlarmPwrLight1_On() 
{
  digitalWrite(pwrLight1Pin, HIGH);
  globalPower.pwrLight1=1;
  if (dispScreen==1) myFiles.load(178, 121, 24, 24, pwrLightIconS[globalPower.pwrLight1]);
}
void AlarmPwrLight1_Off()
{
  digitalWrite(pwrLight1Pin, LOW);
  globalPower.pwrLight1 = 0;
  if (dispScreen==1) myFiles.load(178, 121, 24, 24, pwrLightIconS[globalPower.pwrLight1]); // update home screen
}

//===Light2 routines===

void AlarmPwrLight2_On()
{
  digitalWrite(pwrLight2Pin, HIGH);
  globalPower.pwrLight2=1;
  if (dispScreen==1) myFiles.load(206, 121, 24, 24, pwrLightIconS[globalPower.pwrLight2]);
}
void AlarmPwrLight2_Off()
{
  digitalWrite(pwrLight2Pin, LOW);
  globalPower.pwrLight2 = 0;
  if (dispScreen==1) myFiles.load(206, 121, 24, 24, pwrLightIconS[globalPower.pwrLight2]); // update home screen
}

//===CO2 routines===

void AlarmPwrCO2_On()
{
  if((feedingActive==true)&&(feedSetting.pwrCO2==true))
  {
    preFeedPower.pwrCO2 = 1;
  }else
  {
    digitalWrite(pwrCO2Pin, HIGH);
    globalPower.pwrCO2=1;
  }
  //if (dispScreen==1) myFiles.load(206, 177, 24, 24, pwrCO2IconS[globalPower.pwrCO2]);
  if (dispScreen==1) myFiles.load(178, 177, 24, 24, pwrCO2IconS[globalPower.pwrCO2]);//co2/heat swapped
}
void AlarmPwrCO2_Off()
{
  if((feedingActive==true)&&(feedSetting.pwrCO2==true))
  {
    preFeedPower.pwrCO2 = 0;
  }else
  {
    digitalWrite(pwrCO2Pin, LOW);
    globalPower.pwrCO2 = 0;
  }
  //if (dispScreen==1) myFiles.load(206, 177, 24, 24, pwrCO2IconS[globalPower.pwrCO2]); // update home screen
  if (dispScreen==1) myFiles.load(178, 177, 24, 24, pwrCO2IconS[globalPower.pwrCO2]); //co2/heat swapped
}
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

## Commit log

2018-03-23 Update MrAqua.ino
    v2.5.3
    -Fixed feeding restart button to only re-start timer
    -Updated screen setting menu to update brightness as it's changed rather than waiting till it dims and then goes bright at a touch
    [MrAqua.ino]
2018-03-23 Update Touch.ino
    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
    [Touch.ino]
